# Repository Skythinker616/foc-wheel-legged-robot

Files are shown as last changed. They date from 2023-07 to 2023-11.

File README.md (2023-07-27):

<div align=center>
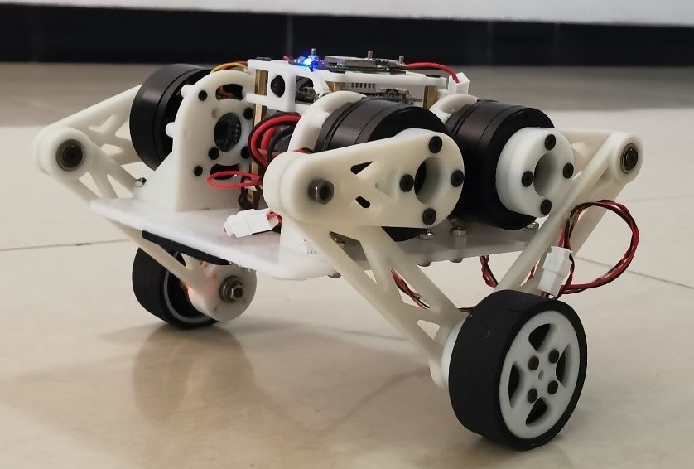
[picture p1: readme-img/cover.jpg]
	
	<h1>FOC 双轮腿机器人项目</h1>
	<p>
		<a href="https://gitee.com/skythinker/foc-wheel-legged-robot">
			
		</a>
		
		<a href="https://github.com/Skythinker616/foc-wheel-legged-robot">
			
		</a>
		
		<a href="https://www.bilibili.com/video/BV1bP411k75b">
			
		</a>
		
	</p>
	<p>
		<b>简体中文 | <a href="README_en.md">English</b></a>
	</p>
</div>

这是一个完整的机器人项目，包含算法仿真、机械结构设计、电子硬件设计、嵌入式软件设计、上位机软件设计等多个部分，完成了以下内容：

- 使用 SolidWorks 完成的机械结构设计
- 基于 MATLAB / Simulink / Simscape 的算法设计和机器人物理仿真
- 基于 STM32，使用 CAN 通信的无刷电机驱动板
- 基于 ESP32、MPU6050 的运动控制模块（主控模块）
- 基于 ffmpeg / ffserver 的 Linux 图传模块，使用低耦合可拔插方案
- 支持蓝牙配网的 Android 遥控 APP

**演示&介绍视频：**[https://www.bilibili.com/video/BV1bP411k75b/](https://www.bilibili.com/video/BV1bP411k75b/)

---

## 部分效果展示

**机械结构渲染图：**

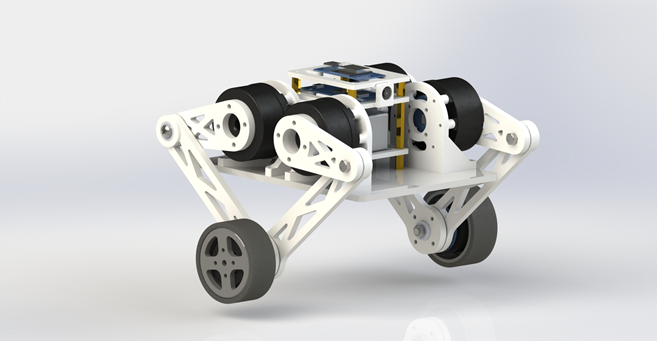
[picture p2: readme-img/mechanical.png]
渲染图


**Simscape Multibody 仿真效果：**

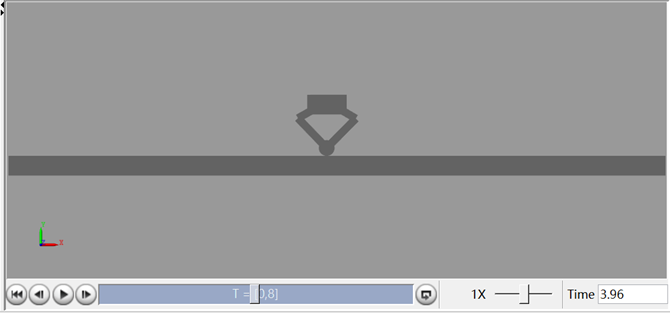
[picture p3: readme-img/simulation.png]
仿真


**机器人加速过程：**

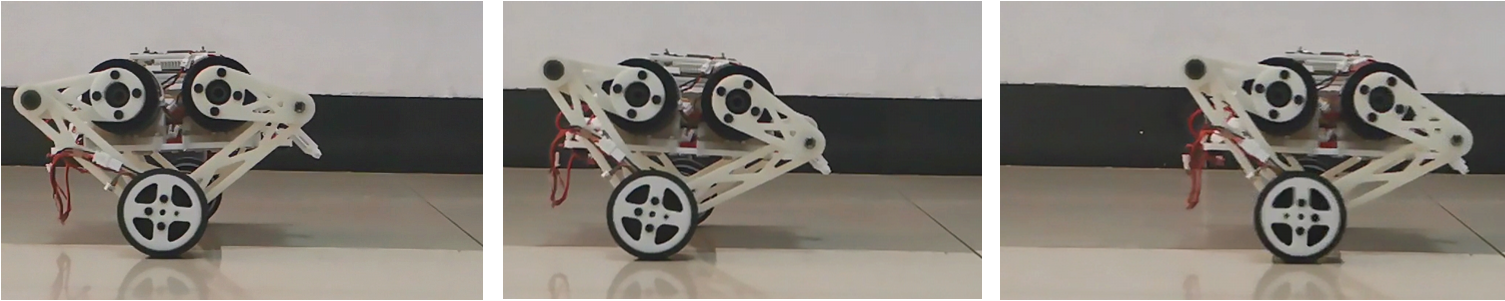
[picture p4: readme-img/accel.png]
加速


**跌落缓冲效果：**

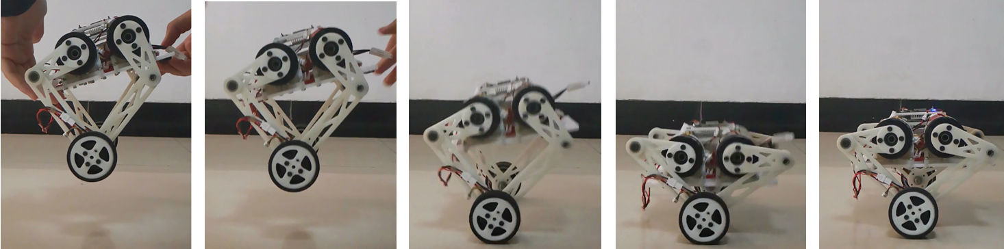
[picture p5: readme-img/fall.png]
跌落


**遥控APP界面：**

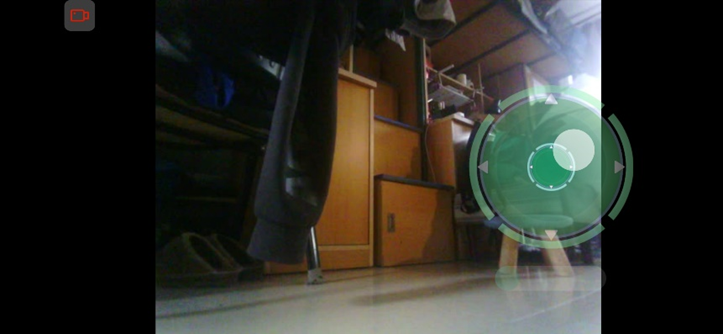
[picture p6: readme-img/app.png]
App


---

## 文件结构

整个机器人项目被分成如下的几个部分，分别位于仓库不同目录下，内部有更详细的说明，读者可以按需查看：

- [`solidworks`](solidworks)：机械结构设计，包含所有零件和总装配体模型文件
- [`matlab`](matlab)：算法仿真，包含模型建立、算法设计和仿真文件等
- [`stm32-foc`](stm32-foc)：无刷电机驱动板，包含硬件设计文件和STM32代码工程
- [`esp32-controller`](esp32-controller)：运动控制模块，包含硬件设计文件和ESP32代码工程
- [`linux-fpv`](linux-fpv)：Linux 图传模块，包含相关Shell脚本和Python脚本
- [`android`](android)：Android 遥控 APP，包含源代码和已编译好的安装包

> 注：图传模块为可选模块，增加可玩性的同时也会明显增加项目的成本和复杂度，删去后其他功能仍可以正常使用

---

## 物料成本

| 项目 | 数量 | 单价 | 总价 |
| :--: | :--: | :--: | :--: |
| 4010电机 | 4 | ￥50.00 | ￥200.00 |
| 2804电机 | 2 | ￥13.00 | ￥26.00 |
| 驱动板元件 | 6 | ￥25.00 | ￥150.00 |
| 主控板元件 | 1 | ￥20.00 | ￥20.00 |
| 航模锂电 | 1 | ￥28.00 | ￥28.00 |
| 3D打印件 | - | 约￥100.00 | 约￥100.00 |
| 定制亚克力 | 1 | ￥5.00 | ￥5.00 |
| 轴承、螺丝 | - | 约￥20.00 | 约￥20.00 |
| 图传核心板（可选） | 1 | ￥150.00 | ￥150.00 |
| 摄像头（可选） | 1 | ￥20.00 | ￥20.00 |
| **总计（不含图传）** | - | - | **￥549.00** |
| **总计（含图传）** | - | - | **￥719.00** |

> 注：以上为笔者实际购买价格，仅供参考，部分购买链接请在各模块的说明中查看

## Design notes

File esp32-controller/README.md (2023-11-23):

# ESP32 主控板

**简体中文 | [English](README_en.md)**

这是本机器人项目最重要的一个子模块，它的职责是：

- 读取板载陀螺仪数据
- 运行所有运动控制算法，包括平衡算法、腿长控制、roll/yaw控制等
- 通过CAN通信获取电机状态并发送扭矩指令
- 通过低功耗蓝牙接收上位机的遥控指令

---

## 硬件说明

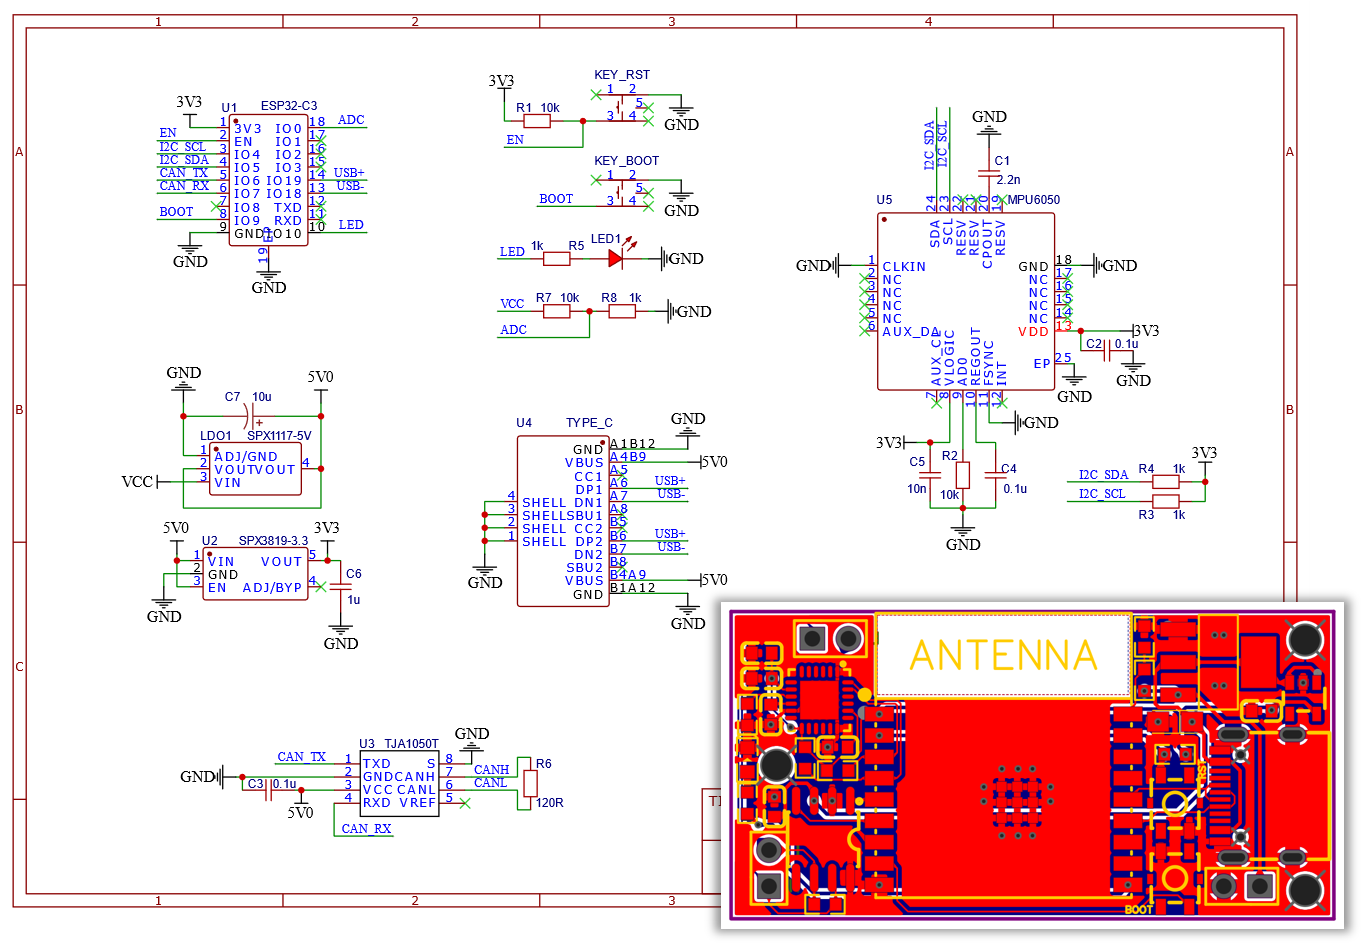
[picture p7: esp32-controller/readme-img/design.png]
电路设计


本模块硬件方案的特性：

- 芯片方案
	- 主控芯片：ESP32-C3
	- 陀螺仪：MPU6050
	- CAN驱动芯片：TJA1050T
- 供电电压：12V，降压方案：LDO
- 调试接口：USB Type-C，直连芯片引脚，可用于烧录程序、JTAG调试和串口通信

### 文件说明

硬件相关文件都在`hardware`目录下：

- `ESP32CTRL_LCEDA_SCH.json`：立创EDA原理图文件
- `ESP32CTRL_LCEDA_PCB.json`：立创EDA PCB文件
- `ESP32CTRL_AD_SCH.schdoc`：立创EDA导出的 Altium Designer 原理图文件
- `ESP32CTRL_AD_PCB.pcbdoc`：立创EDA导出的 Altium Designer PCB文件
- `ESP32CTRL_SVG.svg`：原理图矢量图文件

> 注：将立创原理图和PCB两个json文件导入到[立创EDA标准版](https://lceda.cn/editor)中即可查看和编辑，不建议使用AD

---

## 软件说明

程序使用PlatformIO平台进行开发，使用ESP-IDF并将Arduino框架作为组件引入，因此可同时使用Arduino第三方库和ESP-IDF的底层API(如CAN通信)

为方便程序编写和调试，本程序使用ESP-IDF自带的FreeRTOS进行多任务调度，每个模块会触发一个或多个任务进行处理

### 文件说明

PlatformIO 工程位于`software`目录下，代码文件位于其中`src`目录下：

- `main.cpp`：主要程序文件，包含所有任务模块的逻辑代码
- `PID.c/h`：PID控制器的实现，包含单级和串级PID控制器
- `debug.c/h`：用于[Linkscope](https://gitee.com/skythinker/link-scope)软件实现蓝牙无线调试，不参与正常运行，读者可忽略
- 由MATLAB直接生成的C代码文件，没有可读性，读者可参阅本项目MATLAB程序说明：
	- `leg_pos.c/h`：腿部位置解算函数
	- `leg_spd.c/h`：腿部运动速度解算函数
	- `leg_conv.c/h`：腿部输出换算函数
	- `lqr_k.c/h`：LQR反馈矩阵计算函数

电机、陀螺仪、CAN通信、蓝牙、运动控制等模块的代码全部位于`main.cpp`中（~~其实是偷懒没分开~~），不同模块的函数名基本都以模块名开头，读者可以按此规律参照注释查看

---

## 使用说明

### 烧录程序

使用USB线连接到电脑，按下两个按键后先松开RESET再松开BOOT，芯片即会进入烧录模式，此时可使用PlatformIO进行烧录

### 调试程序

程序中使用Arduinod的Serial类即可从USB输出串口信息，可以使用电脑上的串口调试软件进行查看

此外，ESP32C3的USB还支持JTAG调试，连接到电脑后即可使用[OpenOCD](https://openocd.org/)等程序连接，笔者在调试过程中搭配[Linkscope](https://gitee.com/skythinker/link-scope)实现在线读写变量和曲线绘制，较为方便

### 参数标定

在`main.c`中有几个参数可能需要根据实际系统进行调整，否则将无法进行正确的解算和控制

#### 零点偏移、旋转方向参数

`Motor_InitAll`函数中分别调用`Motor_Init`进行每个电机的参数设定，包括了零点偏移`offsetAngle`和旋转方向`dir`

这两个参数用于在`Motor_Update`函数中将编码器反馈的原始角度转换为算法中的标准角度 $\phi_i$ （电机`angle`成员变量），转换公式为：

$$
\phi_i = (rawAngle_i - offsetAngle_i) * dir_i
$$

这两个参数的测量方法如下：

1. 设置`dir`参数（取值1/-1）使得电机`angle`成员变量在电机向 $\phi_i$ 正方向旋转时增加

2. 程序中设置`offsetAngle=0`（记为 $offsetAngle_i^z$ ），将电机旋转到某个角度，记录当前的计算角度为 $\phi_i^c$ ，测量当前的实际角度为 $\phi_i^r$

3. 将 $\phi_i^c$ 、 $offsetAngle_i^z$ 、 $dir_i$ 代入上方公式，求得 $rawAngle_i$ 的值

4. 将 $\phi_i^r$ 、 $rawAngle_i$ 、 $dir_i$ 代入上方公式，求得 $offsetAngle_i$ 的值，设置到程序中

5. 此时`angle`成员变量应该与实际 $\phi_i$ 一致

> 注1： $\phi_i$ 的定义可以在Matlab程序说明文档中引用的文章中找到，靠前的关节电机对应 $\phi_4$ ，靠后的关节电机对应 $\phi_1$
> 
> 注2：上方描述的均为关节电机，车轮电机仅需设置`dir`参数，使其`angle`变量正方向与算法中驱动轮力矩 $T$ 一致即可

#### 扭矩系数

> 注：若使用笔者相同电机，可以不修改该参数

与上述两个参数相同，该参数也在`Motor_InitAll`函数中进行设置，用于进行电压和扭矩的换算，公式为：

$$
voltage_i = \frac{torque_i}{torqueRatio_i}
$$

其中`torqueRatio`为扭矩系数，其测量方法如下：

1. 给电机不同的电压，测量其扭矩（笔者测的是堵转扭矩），记录为 $(v_i, \tau_i)$
2. 将 $(v_i, \tau_i)$ 拟合为线性函数 $\tau=k*v$ ， $k$ 即为`torqueRatio`的值，可以用Matlab、Excel等软件辅助计算

#### 反电动势函数

> 注：若使用笔者相同电机，可以不修改该参数

关节电机反电动势计算函数为`Motor_CalcRevVolt4010`，车轮电机为`Motor_CalcRevVolt2804`，用于根据电机的实时转速计算反电动势，输出电压指令时会根据计算结果进行补偿，以抵消反电动势

测量反电动势时，给电机不同的电压，测量其空载转速，记录为 $(v_i, \omega_i)$ ，拟合为三次幂函数 $v = f(\omega)$ ，即为反电动势函数

若反电动势标定正确，在设置电机扭矩为0时（`torque`成员为0）手动旋转电机，应该感受到阻力几乎为0（抵消反电动势时顺便抵消了大部分机械阻力）

> 注：注释掉`setup()`中的`Ctrl_Init();`，或注释所有`Motor_SetTorque`函数的调用，即可禁用控制系统的输出，此时可以自行插入代码调试电机

---

## 改进方向

- MPU6050的DMP频率只有200Hz，可以考虑更换其他芯片并编写姿态解算程序
- 硬件使用LDO进行降压，由于ESP32C3功耗较高，LDO发热量较大，可以修改为DC-DC降压
- 关键算法使用MATLAB符号化简结果直接导出，运算量非常大，几乎吃满了芯片性能，无法进一步提升控制频率，可以尝试手动化简后转为C代码

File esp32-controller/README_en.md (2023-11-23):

# ESP32 Main Controller Board

**[简体中文](README.md) | English**

This is the most crucial submodule of the robot project, and its responsibilities include:

- Reading onboard gyroscope data
- Running all motion control algorithms, including balance algorithms, leg length control, roll/yaw control, etc.
- Obtaining motor status via CAN communication and sending torque commands
- Receiving remote control commands from the upper computer through low-power Bluetooth

---

## Hardware Description

Circuit Design

Features of this module's hardware solution:

- Chip Solution
  - Main control chip: ESP32-C3
  - Gyroscope: MPU6050
  - CAN driver chip: TJA1050T
- Power Supply Voltage: 12V, voltage reduction solution: LDO
- Debugging Interface: USB Type-C, directly connected to the chip pins, used for program burning, JTAG debugging, and serial communication

### File Description

Hardware-related files are located in the `hardware` directory:

- `ESP32CTRL_LCEDA_SCH.json`: LCEDA schematic file
- `ESP32CTRL_LCEDA_PCB.json`: LCEDA PCB file
- `ESP32CTRL_AD_SCH.schdoc`: Altium Designer schematic file exported from LCEDA
- `ESP32CTRL_AD_PCB.pcbdoc`: Altium Designer PCB file exported from LCEDA
- `ESP32CTRL_SVG.svg`: Schematic vector file

> Note: Import the two JSON files, the schematic and PCB, into [LCEDA Standard Edition](https://lceda.cn/editor) to view and edit them. It is not recommended to use AD.

---

## Software Description

The program is developed using the PlatformIO platform and uses ESP-IDF, incorporating the Arduino framework as a component. Therefore, it can utilize both Arduino third-party libraries and ESP-IDF's low-level APIs (such as CAN communication).

For ease of program writing and debugging, this program utilizes ESP-IDF's built-in FreeRTOS for multitasking scheduling, and each module will trigger one or more tasks for processing.

### File Description

The PlatformIO project is located in the `software` directory, and the code files are located in the `src` directory:

- `main.cpp`: Main program file, containing the logical code for all task modules
- `PID.c/h`: Implementation of the PID controller, including single-loop and cascade PID controllers
- `debug.c/h`: Used for wireless Bluetooth debugging with [Linkscope](https://gitee.com/skythinker/link-scope) software, not involved in normal operation, readers can ignore it
- C code files generated directly from MATLAB, which are not readable. Readers can refer to the MATLAB program explanation in this project for details:
  - `leg_pos.c/h`: Leg position calculation function
  - `leg_spd.c/h`: Leg motion speed calculation function
  - `leg_conv.c/h`: Leg output conversion function
  - `lqr_k.c/h`: LQR feedback matrix calculation function

The code for motors, gyroscopes, CAN communication, Bluetooth, motion control, and other modules is all located in `main.cpp` (~~I was a bit lazy and didn't separate them~~). The function names of different modules generally start with the module name, and readers can refer to the comments following this pattern to check them.

---

## Instructions for Use

### Program Uploading

Connect the board to the computer via USB, press both buttons, release RESET first, and then release BOOT. The chip will enter the uploading mode, and you can use PlatformIO for uploading.

### Program Debugging

The program uses Arduino's Serial class to output serial information via USB, which can be viewed using serial debugging software on the computer.

In addition, ESP32C3's USB also supports JTAG debugging. After connecting it to the computer, you can use programs like [OpenOCD](https://openocd.org/) to connect. During debugging, I combined it with [Linkscope](https://gitee.com/skythinker/link-scope) for online variable reading, writing, and curve drawing, which is quite convenient.

### Parameter Calibration

Several parameters in `main.c` may need to be adjusted according to the actual system; otherwise, correct computation and control may not be achieved.

#### Zero Offset and Rotation Direction Parameters

In the `Motor_InitAll` function, the `Motor_Init` function is called to set parameters for each motor, including the zero offset `offsetAngle` and rotation direction `dir`.

These two parameters are used in the `Motor_Update` function to convert the raw angle feedback from the encoder to the standard angle $\phi_i$ in the algorithm (motor `angle` member variable). The conversion formula is:

$$
\phi_i = (rawAngle_i - offsetAngle_i) \times dir_i
$$

The measurement methods for these two parameters are as follows:

1. Set the `dir` parameter (values 1/-1) so that the motor `angle` member variable increases when the motor rotates in the positive direction of $\phi_i$.

2. Set `offsetAngle=0` in the program (denoted as $offsetAngle_i^z$), rotate the motor to a certain angle, record the current calculated angle as $\phi_i^c$, and measure the current actual angle as $\phi_i^r$.

3. Substitute $\phi_i^c$, $offsetAngle_i^z$, and $dir_i$ into the above formula to obtain the value of $rawAngle_i$.

4. Substitute $\phi_i^r$, $rawAngle_i$, and $dir_i$ into the above formula to obtain the value of $offsetAngle_i$ and set it in the program.

5. At this point, the `angle` member variable should be consistent with the actual $\phi_i$.

> Note 1: The definition of $\phi_i$ can be found in the article referenced in the Matlab program documentation, where the front joint motor corresponds to $\phi_4$, and the rear joint motor corresponds to $\phi_1`$.
> 
> Note 2: The descriptions above are for joint motors; wheel motors only need to set the `dir` parameter to align their `angle` variable direction with the driving wheel torque $T$ in the algorithm.

#### Torque Coefficient

> Note: If using the same motors as the author, this parameter can be left unchanged.

Similar to the above two parameters, this parameter is also set in the `Motor_InitAll` function and is used for the conversion between voltage and torque. The formula is:

$$
voltage_i = \frac{torque_i}{torqueRatio_i}
$$

Where `torqueRatio` is the torque coefficient, and its measurement method is as follows:

1. Apply different voltages to the motor and measure its torque (the author measured the stall torque), recorded as $(v_i, \tau_i)$.
2. Fit $(v_i, \tau_i)$ to a linear function $\tau=k \times v$. The value of $k$ is the `torqueRatio` and can be calculated using software like Matlab, Excel, etc.

#### Back EMF Function

> Note: If using the same motors as the author, this parameter can be left unchanged.

The back electromotive force calculation function for joint motors is `Motor_CalcRevVolt4010`, and for wheel motors, it is `Motor_CalcRevVolt2804`. It is used to calculate the back electromotive force based on the motor's real-time speed. The output voltage command will be compensated according to the calculation result to counteract the back electromotive force.

When measuring the back electromotive force, apply different voltages to the motor, measure its no-load speed, and record it as $(v_i, \omega_i)$. Fit it to a third-degree polynomial function $v = f(\omega)$, which is the back electromotive force function.

If the back electromotive force calibration is correct, when setting the motor torque to 0 (`torque` member is 0), manually rotating the motor should result in almost zero resistance (when compensating for back electromotive force, most of the mechanical resistance is also compensated).

> Note: Comment out `Ctrl_Init();` in `setup()` or comment out all calls to `Motor_SetTorque` functions to disable the control system's output. This allows for manual insertion of code to debug the motor.

---

## Future Improvements

- The DMP frequency of MPU6050 is only 200Hz; consider replacing it with other chips and writing attitude calculation programs.
- The hardware uses an LDO for voltage reduction, but due to the high power consumption of ESP32C3, the LDO generates a lot of heat. Consider changing to a DC-DC voltage reduction solution.
- Key algorithms directly export results from MATLAB through symbolic simplification, which requires a significant amount of computation and almost saturates the chip's performance, making it impossible to further increase the control frequency. Consider manually simplifying and converting the code to C.

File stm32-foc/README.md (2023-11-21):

# STM32-FOC 电机驱动板

**简体中文 | [English](README_en.md)**

这是本机器人项目的一个子模块，基于 STM32 芯片的无刷电机驱动板，目前有如下特性：

- 芯片方案
	- 主控芯片：STM32F103C6T6
	- 驱动芯片：DRV8313
	- 磁编码器：AS5600
	- CAN驱动芯片：TJA1050T
- 仅支持电压控制扭矩，硬件不支持电流闭环
- 使用 CAN 通信控制（硬件留有串口但程序没有使用）
- 可反馈转角和转速，反馈频率500Hz
- 使用按钮设置电机ID或触发自动标定，产生的参数支持掉电保存
- PCB 尺寸：直径30mm
- 本项目中供电电压：12V
- 物料成本：约￥25

> 注：经测试 STM32F103C8T6 可直接替换，软硬件都可直接兼容

该子模块已经在立创平台开源：[https://oshwhub.com/skythinker/simplefoc103](https://oshwhub.com/skythinker/simplefoc103)

---

## 硬件说明

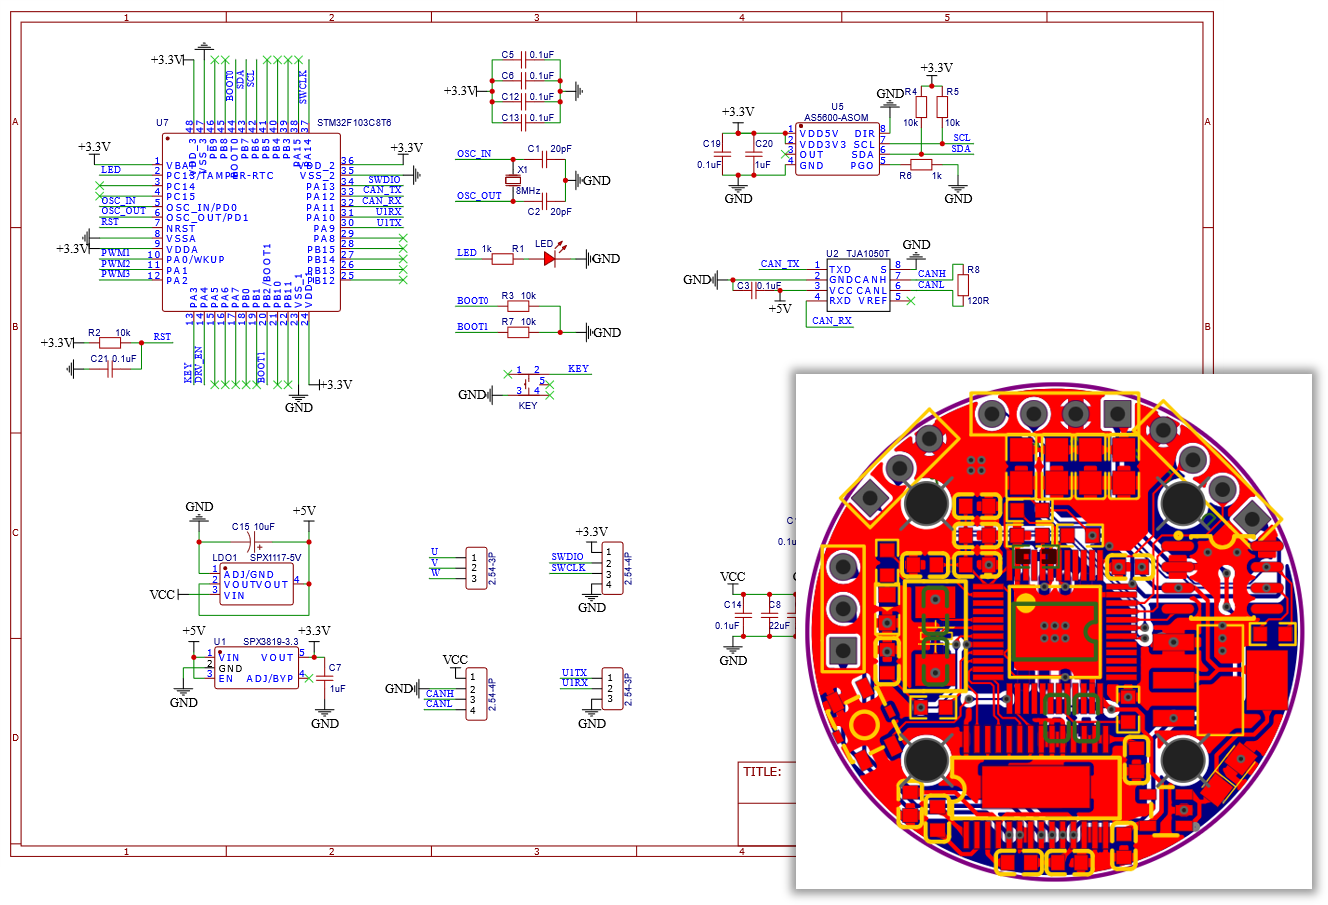
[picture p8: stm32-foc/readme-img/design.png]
电路设计


电路为双层板结构，使用[立创EDA](https://lceda.cn/)设计，其中的对侧打孔相距22mm，与2804电机孔位相同

> 注：程序使用单片机内部RC振荡器，因此外部晶振X1和负载电容C1/C2可以不焊接

### 文件说明

原理图和PCB文件均在`hardware`文件夹中：

- `STM32FOC_LCEDA_SCH.json`：立创EDA原理图文件
- `STM32FOC_LCEDA_PCB.json`：立创EDA PCB文件
- `STM32FOC_AD_SCH.schdoc`：立创导出的 Altium Designer 原理图文件
- `STM32FOC_AD_PCB.pcbdoc`：立创导出的 Altium Designer PCB文件
- `STM32FOC_SVG.svg`：原理图矢量图文件

> 注：将立创原理图和PCB两个json文件导入到[立创EDA标准版](https://lceda.cn/editor)中即可查看和编辑，不建议使用AD

---

## 软件说明

程序开发环境为 Keil uVision 5，使用 STM32CubeMX v5.6.0 生成工程，使用 HAL 库编写

FOC核心算法参考了CSDN博主 [loop222](https://blog.csdn.net/loop222) 所移植的C语言版 SimpleFOC，本程序将其移植到了HAL库中，并添加了CAN通信、Flash掉电存储、蜂鸣、按键、LED、滤波等功能

### 文件说明

`software`文件夹中为STM32代码工程，其中：

- `MDK-ARM/C6T6SimpleFoc.uvprojx`：Keil uVision 5 工程文件
- `C6T6SimpleFoc.ioc`：STM32CubeMX 工程文件
- `Src/main.c`：主要程序代码
- `Src/stm32f1xx_it.c`：各中断服务函数代码
- `USER`目录下为其他工具代码：
	- `BLDCMotor.c/h`、`FOCMotor.c/h`、`foc_utils.c`：FOC算法相关代码
	- `MagneticSensor.c/h`：AS5600磁编码器驱动代码
	- `FlashStorage.c/h`：Flash掉电存储代码

---

## 使用说明

### 硬件设置

1. 将驱动板与电机固定在一起，电机转子上的径向磁铁与磁编码器对正且相距2~3mm

2. 驱动电路板使用2.54mm排针孔引出了电机三相线、CAN总线、电源、SWD调试接口和串口，用户可根据需要自行焊接

	> 注：电源建议选择12V左右，具体范围可以参考DRV8313芯片的电压范围和降压LDO芯片的最高耐压

### 驱动ID设置及自动标定

**驱动ID**：区分一条CAN总线上多个电机的标识，范围1-8，同一总线上的驱动ID不能重复

**自动标定**：驱动需要知道电机的极对数、零点偏移量、传感器方向信息，这些信息可以通过自动标定获得

- 在正常运行状态下，LED的闪烁代表电机当前ID
- 按下按钮不松手即可进入ID设置，此时LED会以500ms周期闪烁，闪烁第N次时松手即可设置ID为N
- 闪烁次数超过8次仍不松手，LED会常亮2秒，此时松手即可进入自动标定
- 若2秒后仍然不松手，LED会熄灭，此后松手不会触发任何操作
- 自动标定时，电机会缓慢旋转，需确保电机处于空载状态，尽可能减少旋转阻力，标定成功后会播放开机音效

### CAN通信协议

CAN通信使用标准帧，波特率为1Mbps

**驱动反馈数据帧格式**：

不同ID的驱动板会使用不同的CAN数据帧标识符(StdID)发送反馈数据：

| 驱动ID | StdID | 帧类型 | DLC |
| :---: | :---: | :----: | :-: |
| N | 0x100+N | 标准帧 | 8 |

| DATA[0-3] | DATA[4-5] | DATA[6-7] |
| :---: | :---: | :---: |
| 累计转角*1000 | 当前转速*10 | 保留 |
| 单位rad | 单位rad/s | / |
| int32_t | int16_t | / |

**驱动板接收电压指令数据帧格式**：

为节省总线带宽，不同ID的驱动板不会使用完全不同的数据帧接收数据，而是共用一个数据帧中的不同字节

共用接收数据帧 **StdID = 0x100** 的四个驱动ID为1-4：

| DATA[0-1] | DATA[2-3] | DATA[4-5] | DATA[6-7] |
| :---: | :---: | :---: | :---: |
| ID=1 输出电压 | ID=2 输出电压 | ID=3 输出电压 | ID=4 输出电压 |
| 单位mV | 单位mV | 单位mV | 单位mV |
| int16_t | int16_t | int16_t | int16_t |

共用接收数据帧 **StdID = 0x200** 的四个驱动ID为5-8：

| DATA[0-1] | DATA[2-3] | DATA[4-5] | DATA[6-7] |
| :---: | :---: | :---: | :---: |
| ID=5 输出电压 | ID=6 输出电压 | ID=7 输出电压 | ID=8 输出电压 |
| 单位mV | 单位mV | 单位mV | 单位mV |
| int16_t | int16_t | int16_t | int16_t |

也就是说，如果向总线发送StdID=0x100的数据帧，那么ID为1-4的驱动板会同时接收到指令；如果发送StdID=0x200的数据帧，则ID为5-8的驱动板会收到指令

> 注意：上述输出电压均为有效值而非峰值，例如供电电压12V时，输出电压允许范围为[0, 6.93V] (12 / √3 = 6.93)

---

## 改进方向

- AS5600磁编码器数据不够稳定，采样频率也不够高(软件IIC实测最高约2KHz)，留给滤波算法的余地不大，可以考虑更换更好的编码器

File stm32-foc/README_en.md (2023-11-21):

# STM32-FOC Motor Driver Board

**[简体中文](README.md) | English**

This is a submodule of the robot project, which is a brushless motor driver board based on the STM32 chip. It currently has the following features:

- Chip solution
  - Main control chip: STM32F103C6T6
  - Driver chip: DRV8313
  - Magnetic encoder: AS5600
  - CAN driver chip: TJA1050T
- Only supports voltage-controlled torque; hardware does not support current closed-loop control
- Uses CAN communication for control (UART is available on the hardware but not utilized in the program)
- Can provide feedback on position and speed with a feedback frequency of 500Hz
- Supports setting the motor ID through a button or triggering automatic calibration, and the generated parameters are saved in non-volatile memory
- PCB size: diameter of 30mm
- Power supply voltage used in this project: 12V
- Material cost: approximately ￥25

> Note: STM32F103C8T6 can be directly replaced and is fully compatible in both software and hardware, as tested.

This submodule has been open-sourced on the oshwhub platform: [https://oshwhub.com/skythinker/simplefoc103](https://oshwhub.com/skythinker/simplefoc103)

---

## Hardware Description

Circuit Design

The circuit is a double-layer board design created using [LCEDA](https://lceda.cn/). The opposite side drilling is spaced at 22mm, which is the same as the 2804 motor mounting holes.

> Note: The program uses the internal RC oscillator of the microcontroller, so the external crystal X1 and load capacitors C1/C2 can be left unpopulated.

### Files Description

The schematic and PCB files are located in the `hardware` folder:

- `STM32FOC_LCEDA_SCH.json`: LCEDA schematic file
- `STM32FOC_LCEDA_PCB.json`: LCEDA PCB file
- `STM32FOC_AD_SCH.schdoc`: Altium Designer schematic file exported from LCEDA
- `STM32FOC_AD_PCB.pcbdoc`: Altium Designer PCB file exported from LCEDA
- `STM32FOC_SVG.svg`: Schematic svg file

> Note: Import the two JSON files, the schematic and PCB, into [LCEDA Standard Edition](https://lceda.cn/editor) to view and edit them. It is not recommended to use AD.

---

## Software Description

The program is developed using Keil uVision 5 as the development environment and generated using STM32CubeMX v5.6.0. It is written using the HAL library.

The FOC core algorithm is based on the C-language version of SimpleFOC, originally ported by CSDN blogger [loop222](https://blog.csdn.net/loop222). This program further integrates it into the HAL library and adds features such as CAN communication, flash memory for non-volatile storage, buzzer, buttons, LEDs, and filtering.

### Files Description

The `software` folder contains the STM32 code project, which includes the following files:

- `MDK-ARM/C6T6SimpleFoc.uvprojx`: Keil uVision 5 project file
- `C6T6SimpleFoc.ioc`: STM32CubeMX project file
- `Src/main.c`: Main program code
- `Src/stm32f1xx_it.c`: Interrupt service routine code
- `USER` folder contains other utility code:
  - `BLDCMotor.c/h`, `FOCMotor.c/h`, `foc_utils.c`: FOC algorithm related code
  - `MagneticSensor.c/h`: AS5600 magnetic encoder driver code
  - `FlashStorage.c/h`: Flash non-volatile memory storage code

---

## Usage Instructions

### Hardware Setup

1. Fix the driver board and the motor together, align the radial magnet on the motor rotor with the magnetic encoder, and keep a distance of 2-3mm.

2. The driver board uses 2.54mm pitch pin headers to expose motor three-phase lines, CAN bus, power supply, SWD debugging interface, and UART. Users can solder them as needed.

> Note: The recommended power supply voltage is around 12V, and the specific range can be referred to the voltage range of the DRV8313 chip and the maximum withstand voltage of the step-down LDO chip.

### Driver ID Setting and Automatic Calibration

**Driver ID**: This is an identifier that distinguishes multiple motors on the same CAN bus, ranging from 1 to 8. The driver IDs on the same bus must not be duplicated.

**Automatic Calibration**: The driver needs to know the pole pairs, zero offset, and sensor direction information of the motor. These pieces of information can be obtained through automatic calibration.

- In normal running state, the LED will blink to indicate the current motor ID.
- To set the ID, press and hold the button. The LED will blink at a 500ms interval. Release the button when the LED blinks for the N-th time to set the ID as N.
- If the button is held for more than 8 blinks, the LED will remain lit for 2 seconds, indicating that automatic calibration will be triggered after releasing the button.
- If the button is not released after 2 seconds, the LED will turn off, and releasing the button will not trigger any action.
- During automatic calibration, the motor will rotate slowly. Ensure that the motor is in an unloaded state and reduce rotational resistance as much as possible. Upon successful calibration, a startup sound effect will be played.

### CAN Communication Protocol

CAN communication uses standard frames with a baud rate of 1Mbps.

**Driver Feedback Data Frame Format**:

Different driver boards with distinct IDs will use different CAN data frame identifiers (StdID) to send feedback data:

| Driver ID | StdID | Frame Type | DLC |
| :---: | :---: | :---: | :-: |
| N | 0x100+N  | Standard | 8 |

| DATA[0-3] | DATA[4-5] | DATA[6-7] |
| :---: | :---: | :---: |
| Accumulated angle \* 1000 | Current speed \* 10 | Reserved |
| Unit: rad | Unit: rad/s | / |
| int32_t | int16_t | / |

**Driver Board Receiving Voltage Command Data Frame Format**:

To save bus bandwidth, driver boards with different IDs will not use entirely different data frames to receive data. Instead, they share the same data frame with different bytes.

The four driver IDs (1-4) share the receive data frame **StdID = 0x100**:

| DATA[0-1] | DATA[2-3] | DATA[4-5] | DATA[6-7] |
| :---: | :---: | :---: | :---: |
| ID=1 Output Voltage | ID=2 Output Voltage | ID=3 Output Voltage | ID=4 Output Voltage |
| Unit: mV | Unit: mV | Unit: mV | Unit: mV |
| int16_t | int16_t | int16_t | int16_t |

The four driver IDs (5-8) share the receive data frame **StdID = 0x200**:

| DATA[0-1] | DATA[2-3] | DATA[4-5] | DATA[6-7] |
| :---: | :---: | :---: | :---: |
| ID=5 Output Voltage | ID=6 Output Voltage | ID=7 Output Voltage | ID=8 Output Voltage |
| Unit: mV | Unit: mV | Unit: mV | Unit: mV |
| int16_t | int16_t | int16_t | int16_t |

In other words, if a data frame with StdID=0x100 is sent on the bus, driver boards with IDs 1-4 will simultaneously receive the command. If a data frame with StdID=0x200 is sent, driver boards with IDs 5-8 will receive the command.

> Note: The above mentioned output voltages are RMS values, not peak values. For example, when the supply voltage is 12V, the allowable range for the output voltage is [0, 6.93V] (12 / √3 = 6.93).

---

## Areas for Improvement

- The AS5600 magnetic encoder data is not stable, and the sampling frequency is not high enough (software I2C measured at a maximum of about 2KHz), leaving little room for filtering algorithms. Consider replacing it with a better encoder.

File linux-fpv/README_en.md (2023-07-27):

# Linux Image Transmission System

**[简体中文](README.md) | English**

This is an optional subsystem in the Robot project, developed on the NanoPI Duo2 development board.

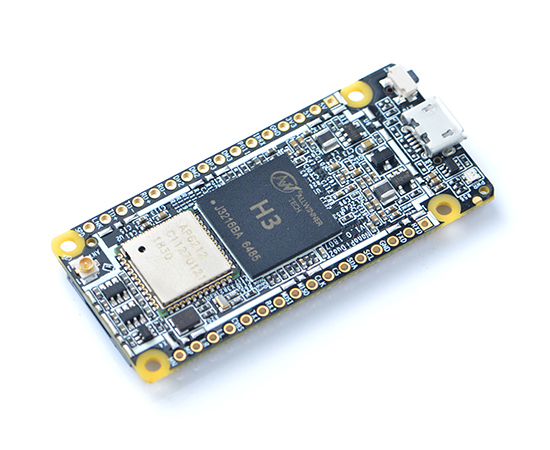
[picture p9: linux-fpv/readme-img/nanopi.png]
NanoPI


The NanoPI Duo2 is a tiny Linux core board measuring 55 x 25.4mm, powered by the Allwinner H3 chip. It supports WiFi and low-power Bluetooth, has a camera interface, and can run either FriendlyCore (based on UbuntuCore) or FriendlyWrt (based on OpenWrt) systems.

The image transmission module of this project is based on the FriendlyCore system (Ubuntu 20.04) of NanoPI Duo2, and it implements the following features:

- Capturing video streams from the ov5640 camera and compressing them into MJPEG format using ffmpeg.
- Streaming the above video stream over HTTP protocol via ffserver for viewing on a mobile app.
- Cooperating with a mobile app to implement Bluetooth pairing, enabling various network connections through the app.
- Creating a UDP server to connect with the mobile app and a Bluetooth GATT client to connect with the main control module, enabling bidirectional data transmission for remote control.

---

## Connection Scheme

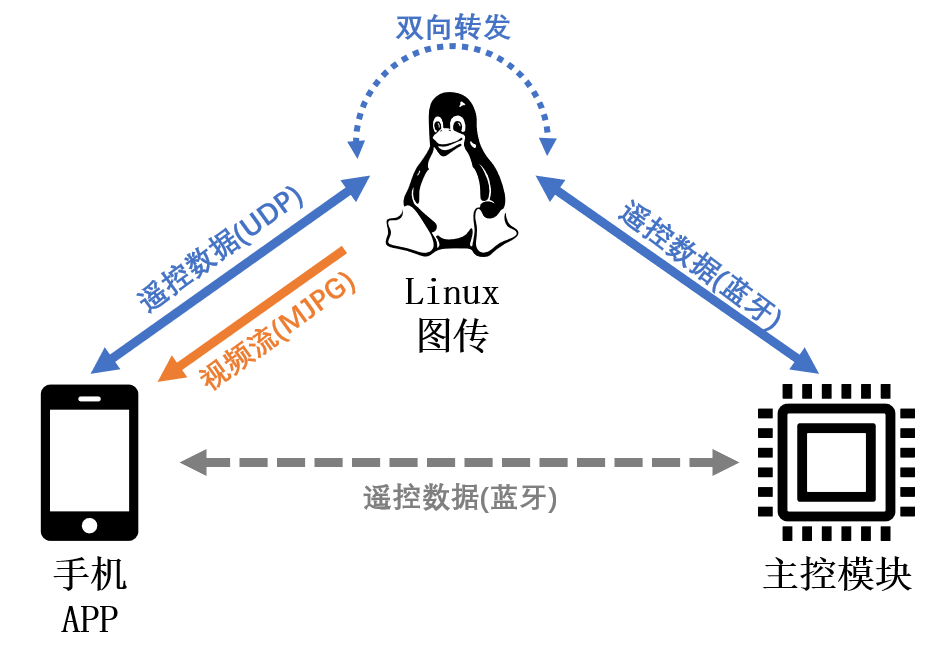
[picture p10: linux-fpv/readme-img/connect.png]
Connection Scheme


The image transmission module implements the plug-and-play scheme shown in the figure above:

- In the scenario of **not using the image transmission system**, the mobile app communicates directly with the main control module via Bluetooth for remote control data transmission (gray arrow).
- In the scenario of **using the image transmission system**, the image transmission system connects with the mobile app through a local area network (LAN) while also connecting with the main control module via Bluetooth. It streams the video (orange arrow) and forwards the remote control data received from the mobile app on the LAN to the main control module (blue arrow). In this case, the robot does not need to be within the range of the mobile app's Bluetooth; it only requires the mobile app and the image transmission system to be on the same LAN.

These two scenarios do not make any difference to the main control module, allowing for flexible switching between different scenarios or complete removal of the image transmission module.

---

## Reference Purchasing Links

> Note: The links below were valid at the time of writing and are for reference only. The availability may vary.

| Item | Purchase Link | Reference Price |
| :--- | :---: | :---: |
| NanoPI Duo2 | [Link](https://item.taobao.com/item.htm?spm=a1z09.2.0.0.67002e8dunEQwK&id=669016013822) | ￥155.00 |
| ov5640 Camera | [Link](https://item.taobao.com/item.htm?spm=a1z09.2.0.0.67002e8dunEQwK&id=676065308445) | ￥20.00 |

---

## Setup Instructions

### 1. Install FriendlyCore System

1. Follow the [official documentation](https://wiki.friendlyelec.com/wiki/index.php/NanoPi_Duo2/zh) to flash the system firmware. The author installed FriendlyCore, based on Linux kernel version 4.14 and Ubuntu 20.04 (focal).

2. Connect the development board to your computer using a USB-to-serial adapter and establish a connection to the board using a serial terminal tool (such as PuTTY). Refer to the official documentation for system login and WiFi network connection.

### 2. Install and Configure ffmpeg and ffserver

1. Download ffmpeg and ffserver from [here](https://ffbinaries.com/downloads). The author used ffmpeg v3.1.4 and ffserver v3.2, and it is recommended to use similar versions.

2. Write the ffserver configuration file by copying the contents from `scripts/ffserver.conf` in this repository to `/etc/ffserver.conf`.

3. Place `scripts/start-ffmpeg.sh` in the system's `/root/balancebot/` directory and run it. Check for any errors. If there are no errors, access `http://<NanoPI's IP address>:8090/camera.mjpg` from another device on the same LAN with a web browser. If you can see the real-time camera stream, the configuration is successful (make sure to connect the camera first).

4. Copy `scripts/mjpg-ffserver.service` to `/lib/systemd/system/` and run the following command:

	```bash
	sudo systemctl daemon-reload
	```

	This will configure the image transmission service as a system service, which can be started or stopped using the following commands:

	```bash
	sudo service mjpg-ffserver start
	sudo service mjpg-ffserver stop
	```

### 3. Configure Python Control Script

1. Ensure that Python 3 is installed on the system. The author used Python 3.8.10 or higher. You can check the Python version using the following command:

	```bash
	python3 --version
	```

2. Install Python dependencies by moving `python/requirements.txt` from the current repository directory to the system, and then run the command:

	```bash
	pip3 install -r requirements.txt
	```

3. Copy the `python/ctrl-proxy.py` file from the repository to the system's `/root/balancebot/` directory. Also, copy the `scripts/ctrl-proxy.service` file to `/lib/systemd/system/`, and run the following command:

	```bash
	sudo systemctl daemon-reload
	```

	This will configure the control script as a system service, which can be started or stopped using the following commands:

	```bash
	sudo service ctrl-proxy start
	sudo service ctrl-proxy stop
	```

4. Set the Python control service to start automatically at boot by running the command:

	```bash
	sudo systemctl enable ctrl-proxy
	```

At this point, the entire image transmission system setup is completed.

---

## Areas for Improvement

- After testing, the current image quality of this solution is 640x480@25fps, and the video delay is approximately 300ms when connected directly to a mobile hotspot. Due to software compression in MJPG format, both CPU and network bandwidth usage are relatively high. You can try using a hardware encoder to compress the video into H264 format and transmit it (the author was not successful in achieving the expected results), or consider using a camera with built-in compression capabilities.

- If image quality is not a concern, you can replace the ffmpeg+ffserver solution with [mjpg-streamer](https://github.com/jacksonliam/mjpg-streamer), which offers easier configuration. However, after testing, it was found that the CPU usage is higher, and without reducing the resolution, it may not achieve a frame rate of 25fps.

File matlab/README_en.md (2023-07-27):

# Model Building & Algorithm Simulation

**[简体中文](README.md) | English**

This project uses MATLAB(R2022b) for the design and simulation of balance algorithms. The main tasks include:

- Leg link posture calculation
- Establishment of the system state space equation
- LQR feedback matrix computation and fitting
- Simscape Multibody physical model construction
- Simulink control algorithm simulation

---

## Control Algorithm

The balance algorithm mainly refers to this [column article](https://zhuanlan.zhihu.com/p/563048952) with only a few differences, hence not elaborated here. It only provides a brief overview of the process, which includes the following steps:

> Note: The variable names in the code remain mostly consistent with those described in the article, and readers can refer to it for comparison.

1. Simplify the leg structure and obtain the mapping relationship between symbols before and after simplification, allowing the calculation of the leg posture using motor data.
2. Determine the mapping relationship between the simplified virtual leg force and the motor torque, enabling control of the simplified leg using the VMC (Virtual Model Control) concept.
3. Conduct classical mechanics analysis and symbolic simplification to obtain the system state space equation.
4. Set the weight coefficients for LQR, calculate the feedback matrix K, and fit the K values for different leg lengths.
5. Implement state feedback control.

---

## File Introduction

- `leg_func_calc.m`: Performs leg kinematics calculations and VMC mapping, which includes steps 1-2 mentioned above, and exports the following three M functions:
	- `leg_pos.m`: Obtains leg posture from joint motor angles.
	- `leg_spd.m`: Obtains leg motion speed from joint motor angles and speeds.
	- `leg_conv.m`: Calculates the torque required by motors from the target torques and thrusts of virtual legs.
- `sys_calc.m`: Computes the system state equation and feedback matrix, which includes steps 3-4 mentioned above, and exports the following M function:
	- `lqr_k.m`: Returns the feedback matrix K corresponding to a specific leg length L0.
- `leg_sim.slx`: Simulink model for leg simulation, including the leg Multibody physical model for verifying the leg VMC algorithm.
	- `leg_sim_2020a.slx`: Exported old version model, suitable for R2020a and above.
- `sys_sim.slx`: Simulink model for the overall balance simulation, including the full robot Multibody physical model for verifying the VMC+LQR overall algorithm.
	- `sys_sim_2020a.slx`: Exported old version model, suitable for R2020a and above.

> Note: The exported M functions are directly used in the simulation model and can be converted to C language using the MATLAB Coder toolbox for direct use in esp32 code. You can find the same-named files in the main control code of this project.

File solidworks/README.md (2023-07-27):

# SolidWorks 机械模型

**简体中文 | [English](README_en.md)**

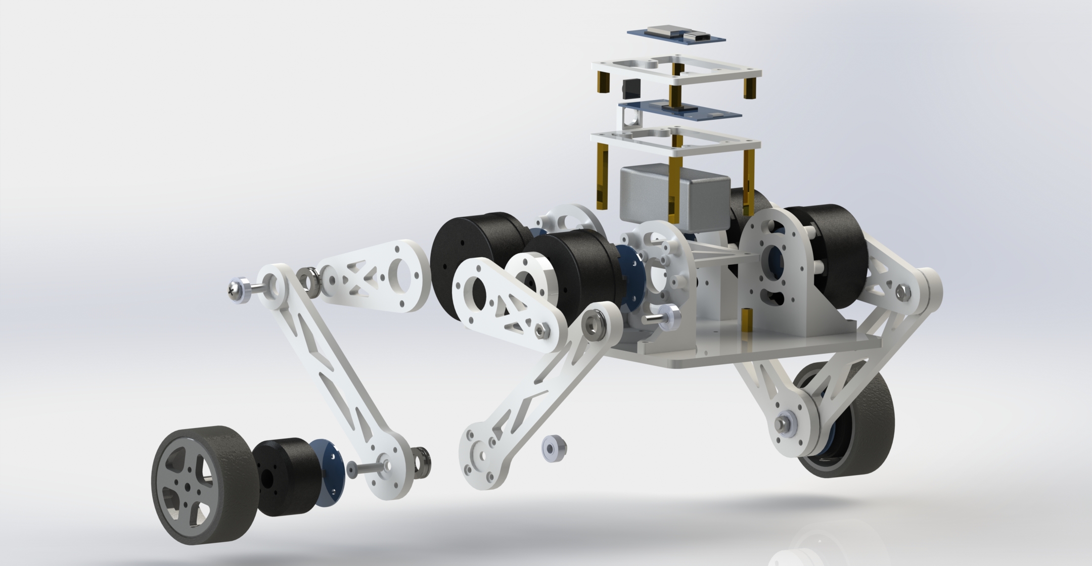
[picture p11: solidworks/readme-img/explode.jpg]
爆炸图


整个机械模型使用SolidWorks 2019 SP0.0设计，当前目录包含所有零件和总装配体`总装.SLDASM`，大部分零件使用3D打印制造，底板为定制亚克力板

---

## 零件选型

> 注：下方的购买链接是笔者当时的购买渠道，仅供参考，不保证可用性

### 电机

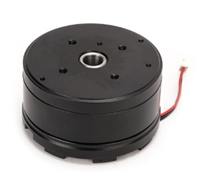
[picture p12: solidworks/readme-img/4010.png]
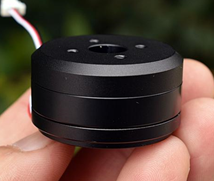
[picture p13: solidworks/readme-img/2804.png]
 

关节电机使用左图所示的4010电机，车轮电机使用右图所示的2804电机，实测电机参数如下：

| 电机型号 | 额定电压 | 堵转扭矩 | 极对数 | 重量 | 购买链接 | 参考价格 |
| :-----: | :---: | :-----: | :----: | :--: | :---: | :---: |
|  4010 |  12V | 0.22N·m | 11 | 125g | [链接](https://item.taobao.com/item.htm?spm=a1z09.2.0.0.67002e8djsrWfk&id=661262833408) | ￥50.00 |
|  2804 |  12V | 0.04N·m | 7 |  24g | [链接](https://item.taobao.com/item.htm?spm=a21n57.1.0.0.54cb523cFK7YX5&id=688692183367) | ￥13.00 |

### 电池

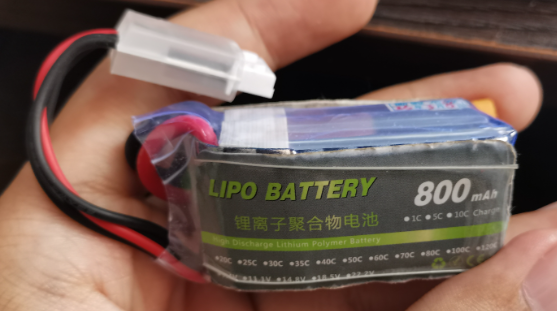
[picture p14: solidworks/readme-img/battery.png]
电池


电池采用了高能量密度高倍率的航模锂电池，实测参数如下：

| 电压 | 容量 | 倍率 | 重量 | 机器人续航 | 购买链接 | 参考价格 |
| :--: | :--: | :--: | :--: | :---: | :---: | :---: |
| 3S (11.1-12.6V) | 800mAh | 25C | 57g | 20-30min | [链接](https://item.taobao.com/item.htm?spm=a1z09.2.0.0.67002e8djsrWfk&id=679306961701) | ￥28.00 | 

### 轴承

在每一个关节处都使用了一个深沟球轴承和一个推力轴承，参数如下：

| 项目 | 内径 | 外径 | 厚度 | 购买链接 | 参考价格 |
| :--: | :--: | :--: | :--: | :---: | :---: |
| 深沟球轴承 604 | 4mm | 12mm| 4mm | [链接](https://item.taobao.com/item.htm?spm=a1z09.2.0.0.67002e8djsrWfk&id=626299304028) | ￥1.30 |
| 推力轴承 F8-14M | 8mm | 14mm | 4mm | [链接](https://item.taobao.com/item.htm?spm=a1z09.2.0.0.67002e8djsrWfk&id=643067962342) | ￥2.00 |

### 螺丝

机器人上使用的大部分都是[扁平头螺丝](https://detail.tmall.com/item.htm?_u=f3m84i7t8421&id=677398679720)，有M2、M2.5、M3、M4几种规格，长度从6mm到16mm不等，有些螺丝没有在模型中画出，需要自行测量（电机上的螺纹盲孔深度为2-3mm）

### 轮胎

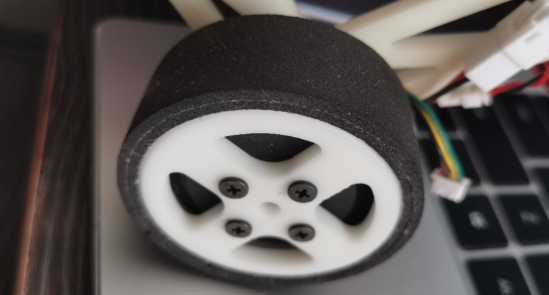
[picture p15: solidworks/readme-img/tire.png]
轮胎


轮胎使用的是自粘海绵胶条，缓冲效果较好，抓地能力较强，但是耐磨性较差，需要定期更换

### 编码器磁铁

电机转子上的磁铁须使用径向充磁的磁铁，由于2804电机不自带磁铁，需要额外设计（本模型选用尺寸直径6mm x 厚度2mm） [购买链接](https://item.taobao.com/item.htm?spm=a1z09.2.0.0.67002e8dunEQwK&id=596454786426) 参考价格：￥6.00 / 5个

### 结构件

机器人底板使用的是白色定制亚克力板 [购买链接](https://detail.tmall.com/item.htm?_u=f3m84i7t207c&id=667937893428) 参考价格：￥5.00

其余全部结构件均在嘉立创使用白色树脂材料打印，全部花费约￥100.00

---

## 改进方向

- 关节电机扭矩无法完成跳跃动作，车轮电机扭矩无法越过较高障碍，可以考虑更换扭矩更大的电机
- 当前电池固定不够牢固，可以增加固定结构
- 车轮电机安装方式 ~~比较阴间~~ 不够方便，可以考虑修改

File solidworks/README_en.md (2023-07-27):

# SolidWorks Mechanical Model

**[简体中文](README.md) | English**

Exploded View

The entire mechanical model is designed using SolidWorks 2019 SP0.0. The current directory contains all parts and the assembly `总装.SLDASM`. Most parts are designed for 3D printing, and the baseplate is made from custom acrylic sheet.

---

## Component Selection

> Note: The purchase links below were used by the author at the time and are provided for reference only. Availability is not guaranteed.

### Motors

 

The articulated joint uses the 4010 motor shown on the left, and the wheel motor uses the 2804 motor shown on the right. The measured motor parameters are as follows:

| Motor Model | Rated Voltage | Stall Torque | Pole Pairs | Weight | Purchase Link | Reference Price |
| :---: | :---: | :---: | :---: | :----: | :---: | :---: |
| 4010 | 12V | 0.22N·m | 11 |  125g  | [Link](https://item.taobao.com/item.htm?spm=a1z09.2.0.0.67002e8djsrWfk&id=661262833408) | ￥50.00 |
| 2804 | 12V | 0.04N·m | 7 |  24g | [Link](https://item.taobao.com/item.htm?spm=a21n57.1.0.0.54cb523cFK7YX5&id=688692183367) | ￥13.00 |

### Battery

Battery

The robot uses a high-energy-density 25C Li-Po batterie. The measured parameters are as follows:

| Voltage | Capacity | Discharge Rate | Weight | Robot Endurance | Purchase Link | Reference Price |
| :-----: | :---: | :---: | :----: | :---: | :---: | :---: |
| 3S (11.1-12.6V) | 800mAh | 25C | 57g  | 20-30min | [Link](https://item.taobao.com/item.htm?spm=a1z09.2.0.0.67002e8djsrWfk&id=679306961701) | ￥28.00 |

### Bearings

A deep groove ball bearing and a thrust bearing are used at each joint, with the following specifications:

| Item | Inner Diameter | Outer Diameter | Thickness | Purchase Link | Reference Price |
| :---: | :---: | :---: | :---: | :---: | :---: |
| Deep Groove Ball Bearing 604 | 4mm | 12mm | 4mm | [Link](https://item.taobao.com/item.htm?spm=a1z09.2.0.0.67002e8djsrWfk&id=626299304028) | ￥1.30 |
| Thrust Bearing F8-14M | 8mm | 14mm | 4mm | [Link](https://item.taobao.com/item.htm?spm=a1z09.2.0.0.67002e8djsrWfk&id=643067962342) | ￥2.00 |

### Screws

Most screws used on the robot are [flat-head screws](https://detail.tmall.com/item.htm?_u=f3m84i7t8421&id=677398679720) with various specifications including M2, M2.5, M3, and M4, with lengths ranging from 6mm to 16mm. Some screws are not depicted in the model and need to be measured independently (the threaded blind holes on the motors are 2-3mm deep).

### Tires

Tire

The robot uses self-adhesive sponge strips as tires, providing good cushioning and strong grip but with relatively poor wear resistance, requiring regular replacement.

### Encoder Magnets

The magnets on the motor rotors must be radially magnetized. Since the 2804 motor does not come with magnets, they need to be designed separately. For this model, magnets with dimensions of 6mm in diameter and 2mm in thickness are used. [Purchase Link](https://item.taobao.com/item.htm?spm=a1z09.2.0.0.67002e8dunEQwK&id=596454786426) Reference Price: ￥6.00 / 5 pieces

### Structural Components

The robot's baseplate is made from custom white acrylic sheet. [Purchase Link](https://detail.tmall.com/item.htm?_u=f3m84i7t207c&id=667937893428) Reference Price: ￥5.00

All other structural components are 3D printed using white resin material from Jialichuang, with a total cost of approximately ￥100.00.

---

## Improvement Directions

- The torque of the articulated joint motor is insufficient for completing jumping actions, and the wheel motor's torque is insufficient for overcoming high obstacles. Consider replacing them with motors having higher torque.
- The current battery fixation is not sturdy enough. Consider adding additional fixation structures.
- The installation method of the wheel motor is not very convenient. Consider making modifications.

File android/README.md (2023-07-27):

# Android App

**简体中文 | [English](README_en.md)**

这是本机器人项目的一个子模块，基于Android Studio开发，有以下功能：

- 读取用户触摸输入，向机器人发送遥控指令
- 拉取图传系统的视频流显示在界面上
- 配合图传系统进行蓝牙配网

界面效果

---

## 实现方案

### 显示方案

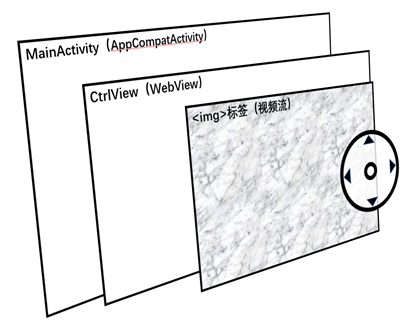
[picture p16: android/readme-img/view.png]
界面层级


由于图传系统传来的MJPG视频流可以直接在各种浏览器中访问，因此本程序直接重写了一个WebView作为主显示视图，仅需编写少量HTML+JavaScript代码即可实现视频流的显示

同时，程序重写了WebView的onDraw方法，在HTML页面上方叠加绘制了摇杆、滑块等控件，并通过onTouchEvent方法监听用户的触摸输入

### 图传连接方案

关于图传系统的通信链路，请先参阅[图传系统方案](../linux-fpv/README.md#连接方案)

为了连接到图传系统，需要通过网络建立视频流连接和UDP遥控数据链接，如下图所示时序：

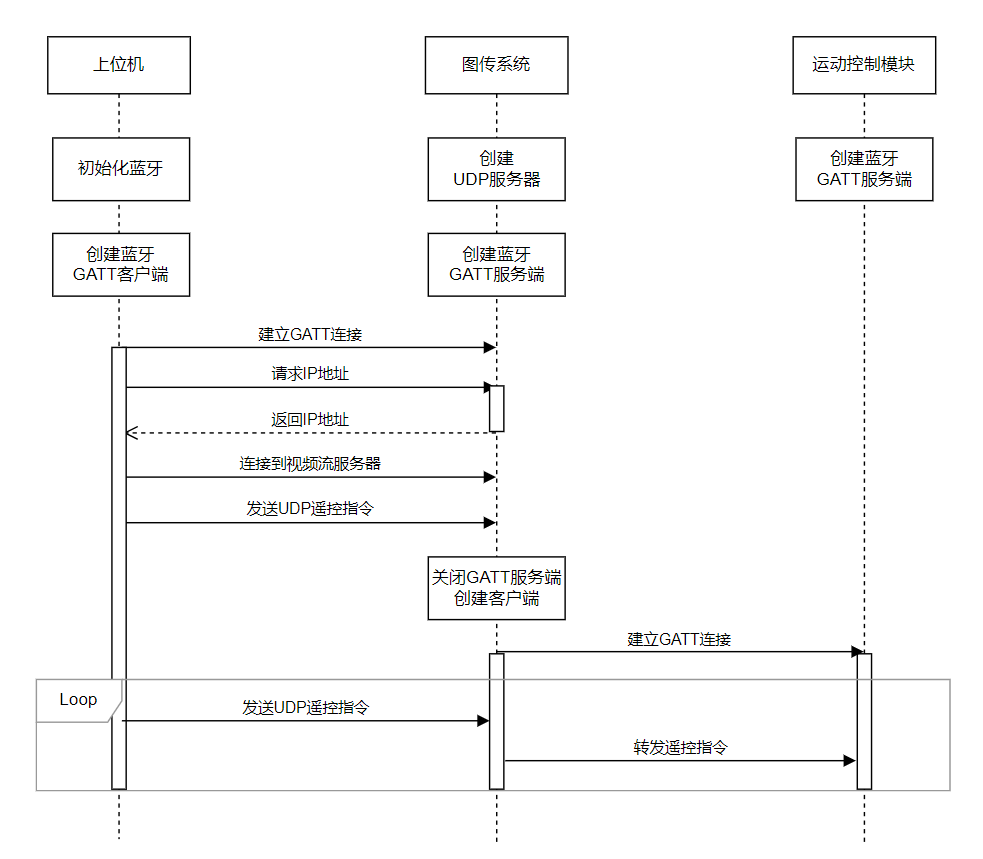
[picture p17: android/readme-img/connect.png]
连接时序


> 注：图中“上位机”表示本程序，“运动控制模块”表示机器人主控模块

### 蓝牙配网方案

蓝牙配网指的是本程序先通过蓝牙直接连接到图传系统，向其发送网络信息，使其连接到指定的WiFi网络，此后即可通过网络连接到图传系统，整个过程都是自动完成的，如下图所示时序：

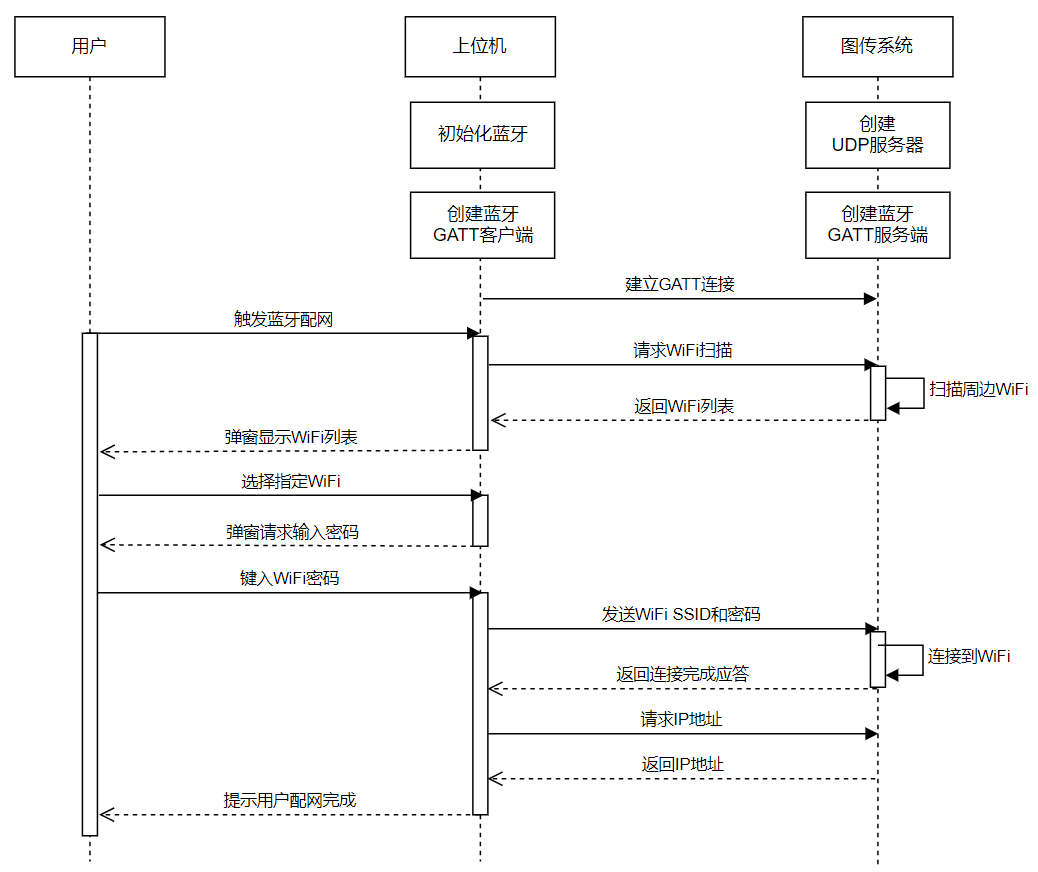
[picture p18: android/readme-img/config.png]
蓝牙配网时序


---

## 主要文件

- `balancebot.apk`：已编译好的安装包，可直接安装
- `app/src/main/java/com/skythinker/balancebot`：Java源代码
	- `MainActivity.java`：主Activity，负责创建各模块对象，接收事件并发送遥控指令
	- `Bluetooth.java`：蓝牙模块，负责蓝牙连接、数据收发
	- `WifiClient.java`：WiFi客户端模块，负责创建UDP客户端并收发数据
	- `CtrlView.java`：主视图，重写自WebView，负责绘制界面
- `app/src/main/AndroidManifest.xml`：Android清单文件，声明了程序的权限和Activity
- `app/src/main/res/drawable`：各图片资源
- `app/src/main/assets/streamview.html`：显示视频流的WebView页面

---

## 使用说明

1. 给机器人上电，等待图传系统启动完成(约1min)

2. 打开本程序，点击左上角的配置按钮

	- 如果不使用图传，点选“切换到蓝牙模式”，等待连接成功
	- 如果使用图传，点选“切换到图传模式”，然后再次点击配置按钮选择“进行连接配置”，按要求选择网络并输入密码，等待连接成功

3. 左上角配置按钮由灰色变亮即表示连接成功，此时即可使用摇杆控制机器人

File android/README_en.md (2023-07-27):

# Android App

**[简体中文](README.md) | English**

This is a sub-module of the Robot Project, developed using Android Studio, and it provides the following functionalities:

- Reads user touch inputs to send remote control commands to the robot.
- Pulls and displays the video stream from the image transmission system on the interface.
- Cooperates with the image transmission system for Bluetooth pairing.

Interface Preview

---

## Implementation Approach

### Display Solution

Interface Hierarchy

Since the MJPG video stream from the image transmission system can be directly accessed in various browsers, this application directly utilizes a WebView as the main display view. Only a small amount of HTML+JavaScript code is needed to display the video stream.

Additionally, the application overrides the onDraw method of WebView to overlay controls such as joystick and sliders on top of the HTML page, and it uses the onTouchEvent method to listen for user touch inputs.

### Image Transmission Connection Solution

Regarding the communication link of the image transmission system, please refer to [Image Transmission System Solution](../linux-fpv/README_en.md#Connection%20Scheme) first.

To connect to the image transmission system, a video stream connection and UDP remote control data link need to be established over the network. The following timing diagram illustrates the process:

Connection Timing

> Note: In the diagram, "Upper Computer" represents this application, and "Motion Control Module" represents the robot's main control module.

### Bluetooth Pairing Solution

Bluetooth pairing refers to this application establishing a direct Bluetooth connection with the image transmission system, sending network information to connect it to the specified WiFi network. Afterward, the application can connect to the image transmission system over the network automatically. The following timing diagram illustrates the process:

Bluetooth Pairing Timing

---

## Important Files

- `balancebot.apk`: Pre-compiled installation package for direct installation.
- `app/src/main/java/com/skythinker/balancebot`: Java source code.
	- `MainActivity.java`: Main Activity responsible for creating various module objects, receiving events, and sending remote control commands.
	- `Bluetooth.java`: Bluetooth module responsible for Bluetooth connection and data transmission.
	- `WifiClient.java`: WiFi client module responsible for creating UDP client and handling data transmission.
	- `CtrlView.java`: Main view, overrides WebView, responsible for UI drawing.
- `app/src/main/AndroidManifest.xml`: Android manifest file, declaring the program's permissions and activities.
- `app/src/main/res/drawable`: Various image resources.
- `app/src/main/assets/streamview.html`: WebView page for displaying the video stream.

---

## Usage Instructions

1. Power on the robot and wait for the image transmission system to start up (approximately 1 minute).

2. Open this application and click the configuration button in the top-left corner.

	- If not using image transmission, select "Switch to Bluetooth mode" and wait for a successful connection.
	- If using image transmission, select "Switch to image transmission mode," then click the configuration button again, and choose "Configure connection" as instructed. Select the network and enter the password as required, and wait for a successful connection.

3. The configuration button in the top-left corner will become active (from gray to lit) when the connection is successful. At this point, you can use the joystick to control the robot.

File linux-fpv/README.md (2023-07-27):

# Linux 图传系统

**简体中文 | [English](README_en.md)**

这是本机器人项目中的一个可选子系统，基于NanoPI Duo2开发板进行开发

NanoPI

这是一块 55 x 25.4mm 的非常小巧的Linux核心板，使用全志H3芯片，支持WiFi和低功耗蓝牙，引出了摄像头接口，可以运行FriendlyCore系统(基于UbuntuCore)或FriendlyWrt系统(基于OpenWrt)

本项目的图传子模块基于其FriendlyCore系统(Ubuntu 20.04)进行开发，实现了以下功能：

- 通过ffmpeg采集ov5640摄像头的视频流并压缩为mjpeg格式
- 通过ffserver将上述视频流以HTTP协议进行推流，以便在手机APP中收看
- 与手机APP配合实现蓝牙配网，在手机端操作即可连接各种网络
- 创建UDP服务端与手机APP连接，创建蓝牙GATT客户端与主控模块连接，实现遥控数据双向转发

---

## 连接方案

连接方案

图传模块实现了上图所示的可拔插方案：

 - 在**不使用图传系统**的情况下，手机APP与主控模块通过蓝牙直连进行遥控数据传输(灰色箭头)
 - 在**使用图传系统**的情况下，图传系统与手机通过局域网连接，同时通过蓝牙与主控模块连接，在传输视频流(橙色箭头)的同时，将手机从局域网传来的遥控数据转发到主控模块(蓝色箭头)。此时机器人不需要在手机蓝牙范围内，仅需保证手机与图传系统在同一局域网内即可

这两种情况对于主控模块没有任何区别，因此可以在不同的场景下灵活切换，也可以完全移除图传模块

---

## 参考购买途径

> 注：下方的链接是笔者当时的购买链接，仅供参考，不保证可用性

| 项目 | 购买链接 | 参考价格 |
| :--: | :---: | :---: |
| NanoPI Duo2 | [链接](https://item.taobao.com/item.htm?spm=a1z09.2.0.0.67002e8dunEQwK&id=669016013822) | ￥155.00 |
| ov5640摄像头 | [链接](https://item.taobao.com/item.htm?spm=a1z09.2.0.0.67002e8dunEQwK&id=676065308445) | ￥20.00 |

---

## 搭建方法

### 1. 安装FriendlyCore系统

1. 参照[官方文档](https://wiki.friendlyelec.com/wiki/index.php/NanoPi_Duo2/zh)进行系统固件的烧录，笔者安装的是基于Linux内核版本4.14和Ubuntu 20.04(focal)的FriendlyCore系统

2. 使用USB转串口模块将开发板连接到电脑，使用串口终端工具(如PuTTY)连接到开发板，参照官方文档登录系统并连接到WiFi网络

### 2. 安装并配置ffmpeg和ffserver

1. 下载ffmpeg和ffserver [下载地址](https://ffbinaries.com/downloads)，笔者使用的是ffmpeg v3.1.4和ffserver v3.2，建议使用相近版本

2. 编写ffserver配置文件，将本仓库目录`scripts/ffserver.conf`中的内容复制到`/etc/ffserver.conf`中

3. 将`scripts/start-ffmpeg.sh`放在系统`/root/balancebot/`目录下并运行，查看是否报错，若不报错，从同一局域网下的其他设备上用浏览器访问`http://<NanoPI的IP地址>:8090/camera.mjpg`，若能看到摄像头的实时画面，则说明配置成功(记得先插上摄像头)

4. 将`scripts/mjpg-ffserver.service`复制到`/lib/systemd/system/`下，运行命令：

	```bash
	sudo systemctl daemon-reload
	```

	即可将图传指令配置为系统服务，可以通过下述命令进行启动或停止
	
	```bash
	sudo service mjpg-ffserver start
	sudo service mjpg-ffserver stop
	```

### 3. 配置Python控制脚本

1. 确定系统已经安装Python3，笔者使用的是Python 3.8.10，建议使用相近或更高版本。可以使用以下命令查看Python版本：

	```bash
	python3 --version
	```

2. 安装Python依赖库，将当前仓库目录下`python/requirements.txt`移至系统中，运行命令：

	```bash
	pip3 install -r requirements.txt
	```

3. 将仓库中`python/ctrl-proxy.py`文件复制到系统`/root/balancebot/`目录下，再将`scripts/ctrl-proxy.service`文件复制到`/lib/systemd/system/`下，运行命令：

	```bash
	sudo systemctl daemon-reload
	```

	即可将该控制脚本配置为系统服务，可以通过下述命令进行启动或停止
	
	```bash
	sudo service ctrl-proxy start
	sudo service ctrl-proxy stop
	```

4. 将Python控制服务设置为开机自启动，运行命令：

	```bash
	sudo systemctl enable ctrl-proxy
	```

此时已经完成整个图传系统的搭建

---

## 改进方向

- 经测试，本方案图传画质为640x480@25fps，直连手机热点时画面延迟约300ms，由于使用软件压缩为MJPG格式，CPU和网络带宽占用都比较高，可以尝试调用硬件编码器压缩为H264格式并传输(笔者没有成功达到预期效果)，或换用内置压缩功能的摄像头

- 不考虑图像画质的话，可以将ffmpeg+ffserver方案直接更换为[mjpg-streamer](https://github.com/jacksonliam/mjpg-streamer)方案，配置更为方便，但经测试CPU占用更高，不降分辨率的话无法达到25fps帧率

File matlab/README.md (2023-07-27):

# 模型搭建&算法仿真

**简体中文 | [English](README_en.md)**

本项目使用 MATLAB(R2022b) 进行平衡算法的设计和仿真，主要进行了：

- 腿部连杆姿态计算
- 系统状态空间方程建立
- LQR 反馈矩阵计算和拟合
- Simscape Multibody 物理模型搭建
- Simulink 控制算法仿真

---

## 控制算法

平衡算法主要参考了这个[专栏文章](https://zhuanlan.zhihu.com/p/563048952)，仅有少许不同，因此不在此处详述，仅描述大致过程，包含以下几个步骤：

> 注：代码中变量名称与该文章所述基本保持一致，读者可以对照查看

1. 对腿部结构进行化简，求得化简前后各符号的对照关系，从而可以使用电机数据计算出腿部的姿态
2. 求得化简后的虚拟腿受力到电机扭矩的映射关系，从而可以使用VMC思想对化简后的腿部进行控制
3. 进行经典力学分析和符号化简，求得系统状态空间方程
4. 设定LQR中的权重系数，求取反馈矩阵K，并对不同腿长求出的K进行拟合
5. 进行状态反馈控制

---

## 文件介绍

- `leg_func_calc.m`：进行腿部解算和 VMC 映射计算，包含上述步骤1-2，导出以下三个M函数：
	- `leg_pos.m`：可由关节电机角度求得腿部姿态
	- `leg_spd.m`：可由关节电机角度速度求得腿部运动速度
	- `leg_conv.m`：可由虚拟腿目标扭矩和推力求得电机所需输出的力矩
- `sys_calc.m`：求得系统状态方程，求得反馈矩阵，包含上述步骤3-4，导出下述M函数：
	- `lqr_k.m`：代入腿长 L0 后返回该腿长对应的反馈矩阵 K
- `leg_sim.slx`：腿部仿真 Simulink 模型，包含腿部 Multibody 物理模型，用于腿部VMC算法验证
	- `leg_sim_2020a.slx`：导出的旧版本模型，适用 R2020a 及以上版本
- `sys_sim.slx`：整机平衡仿真 Simulink 模型，包含整机 Multibody 物理模型，用于 VMC+LQR 整体算法验证
	- `sys_sim_2020a.slx`：导出的旧版本模型，适用 R2020a 及以上版本

> 注：导出的M函数都在仿真模型中直接使用，使用 MATLAB Coder 工具箱直接转换为C语言后即可直接在实机代码中使用，在本项目主控代码中可以找到同名文件

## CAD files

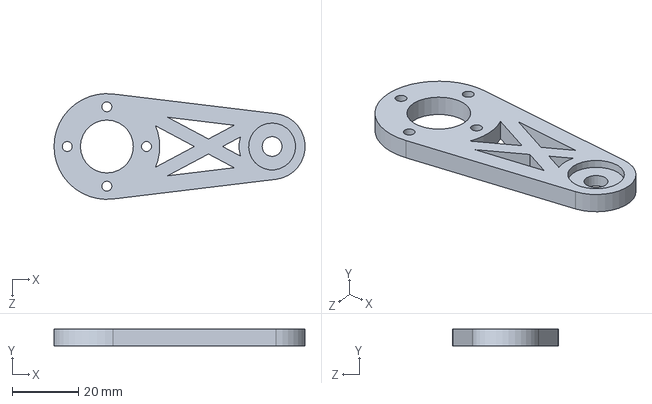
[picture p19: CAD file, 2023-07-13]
solidworks/大腿.SLDPRT
76.0 x 5.00 x 32.0 mm

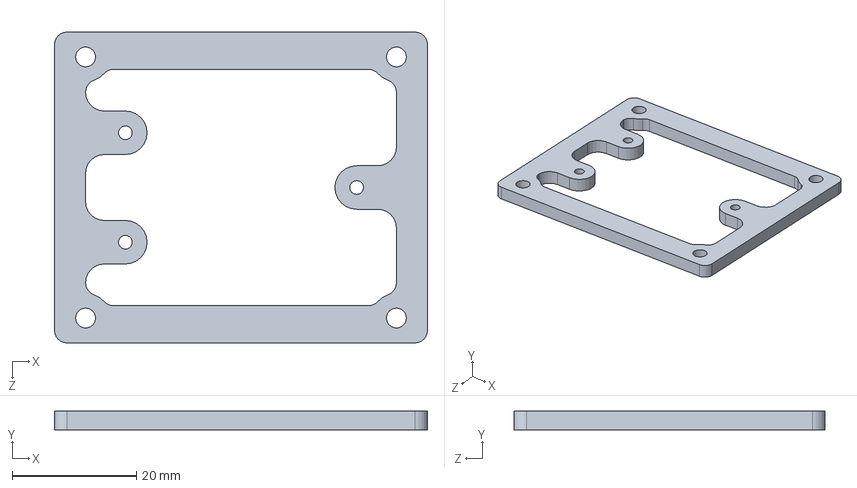
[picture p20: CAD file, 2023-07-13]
solidworks/主控支架.SLDPRT
60.0 x 3.00 x 50.0 mm

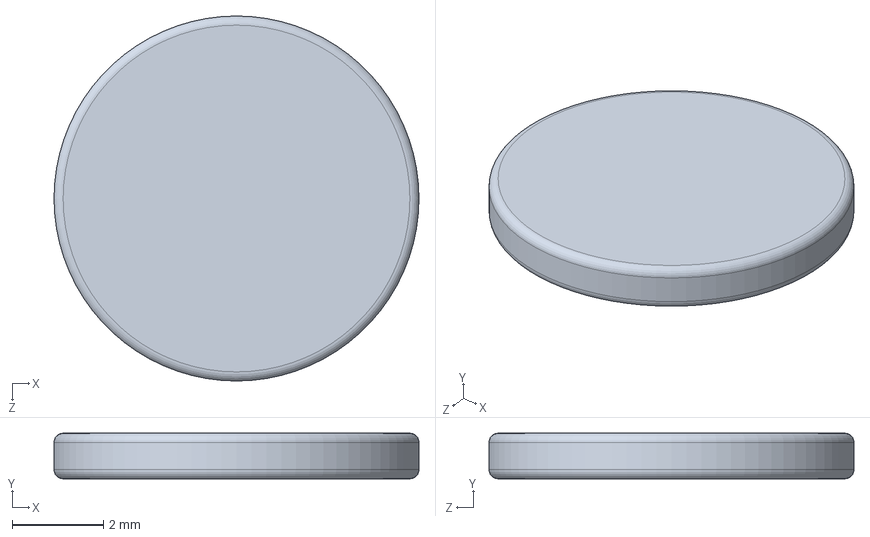
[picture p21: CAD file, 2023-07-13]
solidworks/编码器磁铁.SLDPRT
8.00 x 1.00 x 8.00 mm

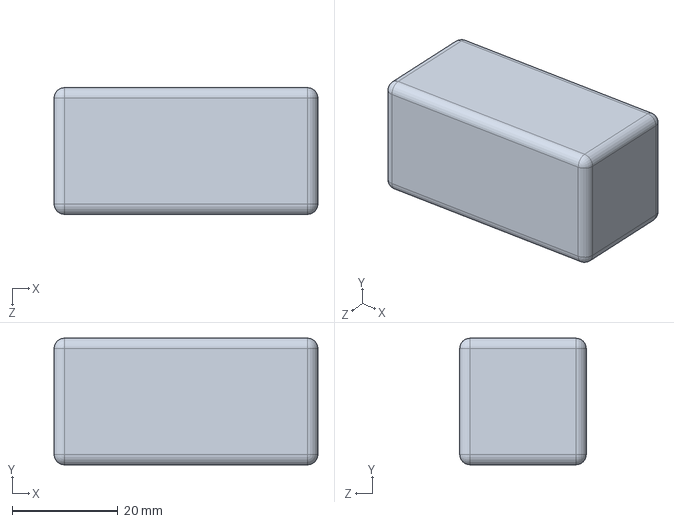
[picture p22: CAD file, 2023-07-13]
solidworks/动力锂电池.SLDPRT
50.0 x 24.0 x 24.0 mm

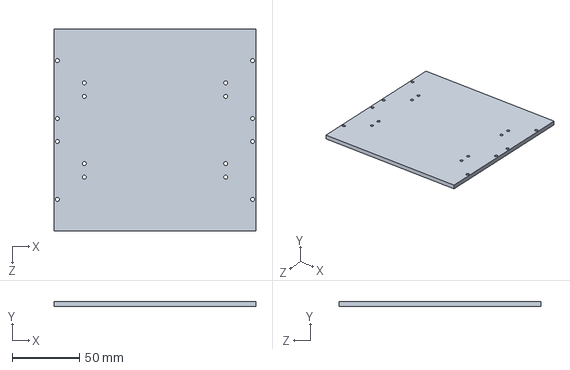
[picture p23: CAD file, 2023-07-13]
solidworks/底板.SLDPRT
150.0 x 4.00 x 150.0 mm

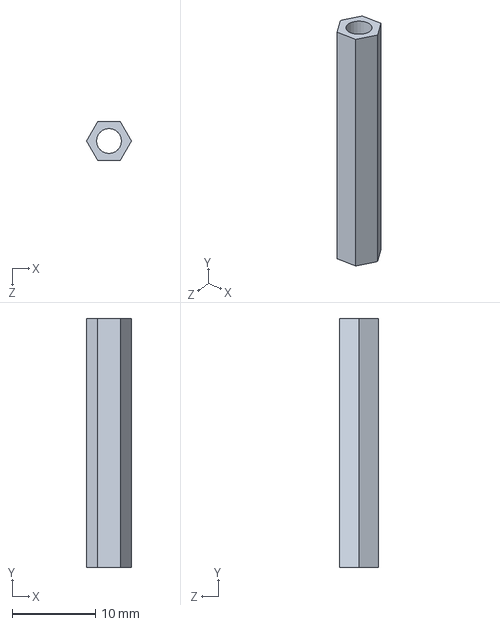
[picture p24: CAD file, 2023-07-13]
solidworks/主控支撑铜柱.SLDPRT
5.43 x 30.0 x 4.70 mm

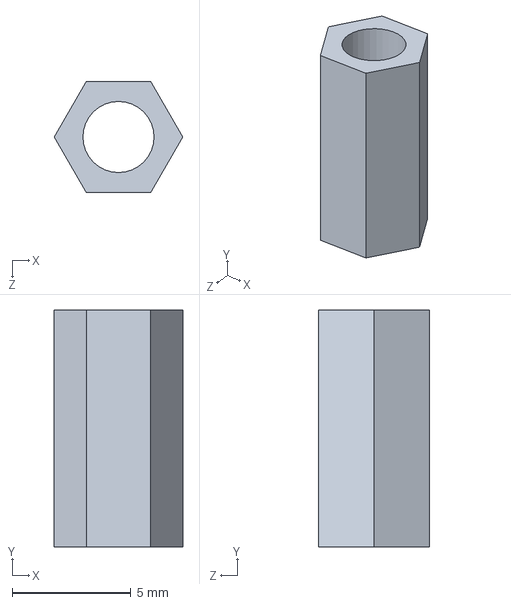
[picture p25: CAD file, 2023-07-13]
solidworks/电池支撑铜柱.SLDPRT
5.43 x 10.0 x 4.70 mm

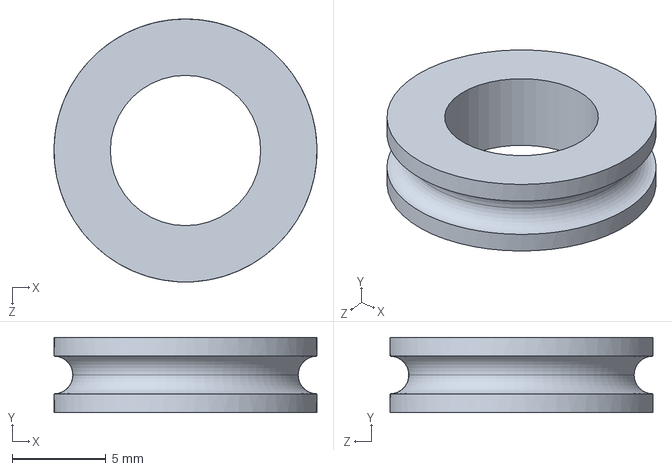
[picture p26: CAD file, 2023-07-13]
solidworks/推力轴承.SLDPRT
14.0 x 4.00 x 14.0 mm

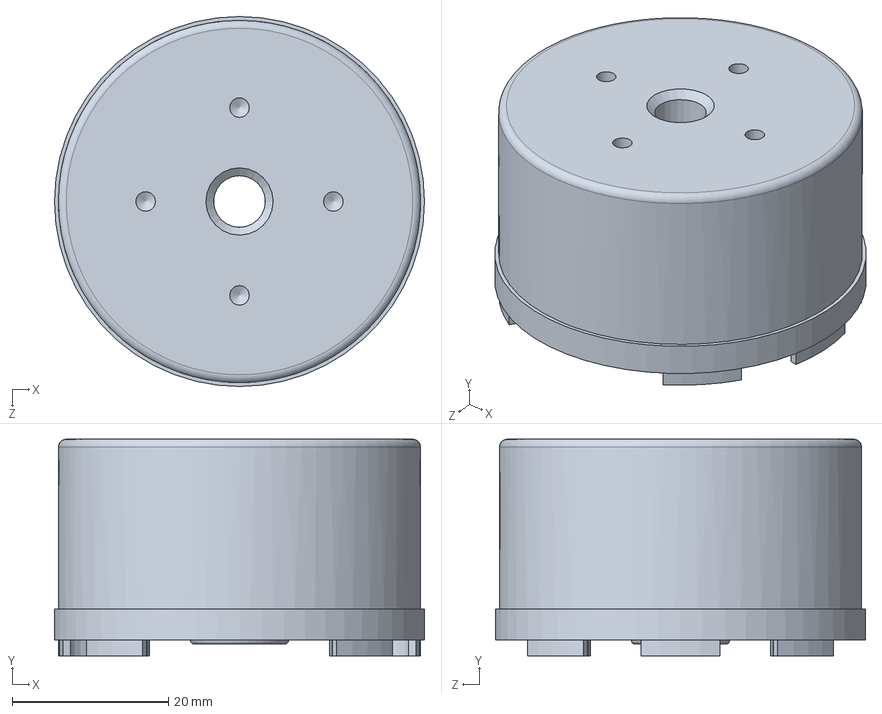
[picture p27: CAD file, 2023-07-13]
solidworks/4010电机.SLDPRT
47.3 x 27.7 x 47.3 mm

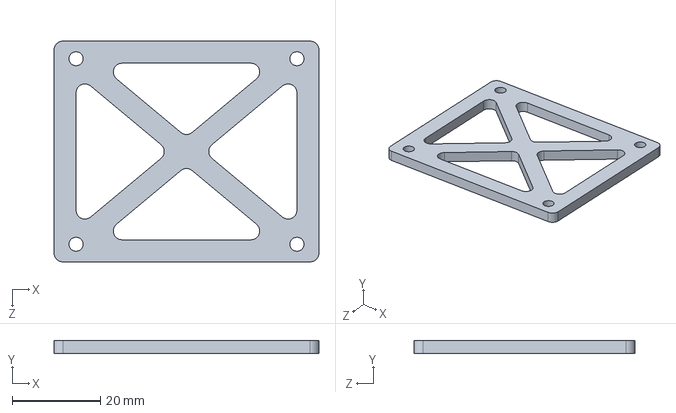
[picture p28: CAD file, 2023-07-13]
solidworks/电池架.SLDPRT
60.0 x 3.00 x 50.0 mm

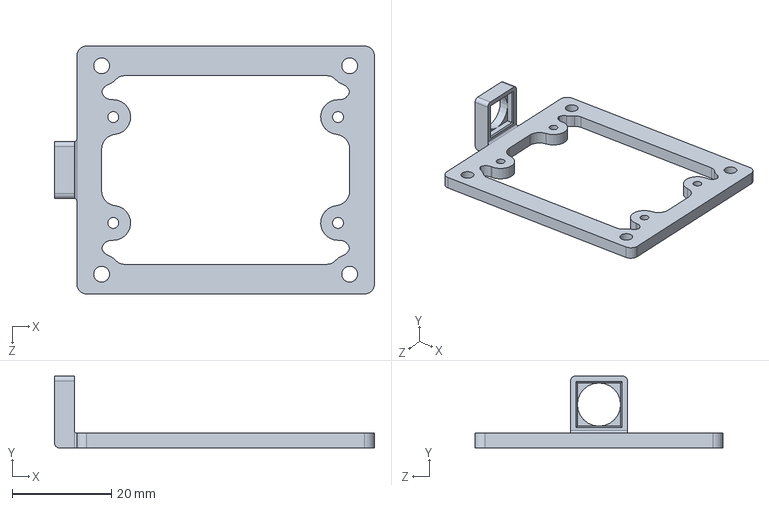
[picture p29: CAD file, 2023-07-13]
solidworks/NanoPi支架.SLDPRT
64.5 x 14.5 x 50.0 mm

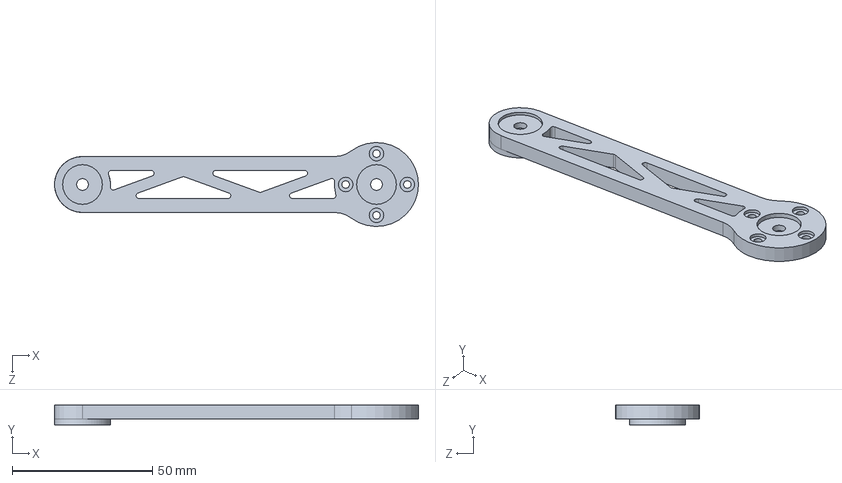
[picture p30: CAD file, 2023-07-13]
solidworks/小腿.SLDPRT
130.0 x 7.00 x 30.0 mm

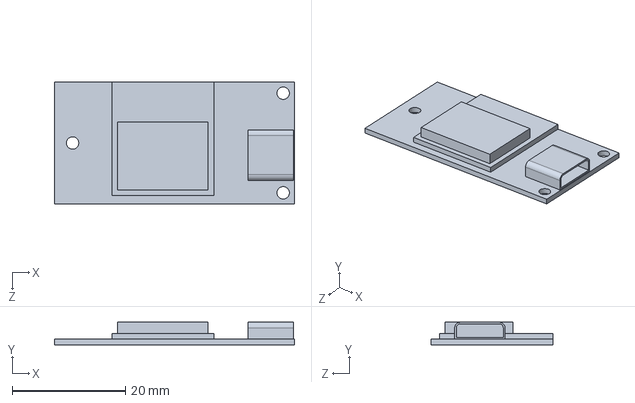
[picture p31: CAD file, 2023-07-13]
solidworks/主控板PCB.SLDPRT
42.4 x 4.00 x 21.6 mm

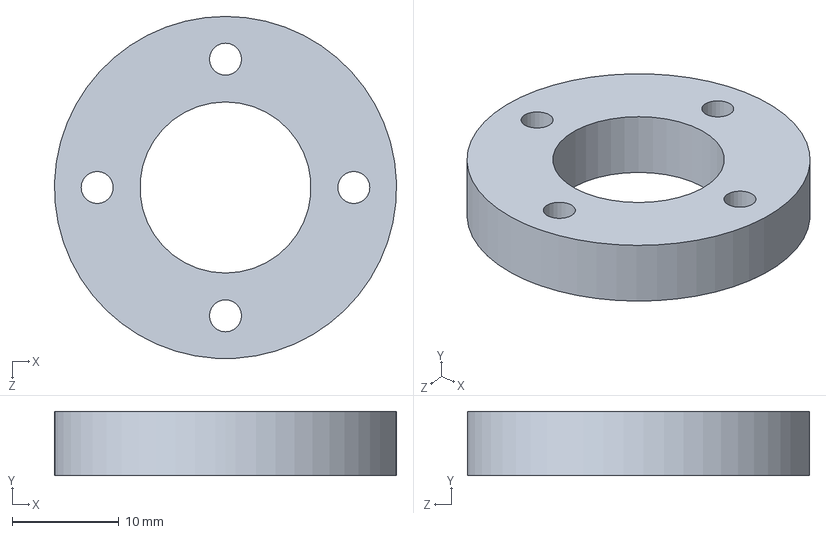
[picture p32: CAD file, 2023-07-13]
solidworks/大腿垫高.SLDPRT
32.0 x 6.00 x 32.0 mm

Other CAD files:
solidworks/OV5640镜头.SLDPRT
solidworks/hex nuts, style 1-grades ab gb.sldprt
solidworks/车轮.SLDPRT
solidworks/2804电机.SLDPRT
solidworks/MISUMI_C-SE604ZZ_不锈钢小径滚珠轴承.SLDPRT
solidworks/MISUMI_CBSTSR4-16_内六角螺栓（盖螺栓）.SLDPRT
solidworks/NanoPi.SLDPRT
solidworks/cross recessed pan head screws gb.sldprt
solidworks/关节电机支架.SLDPRT
solidworks/轮胎.SLDPRT
solidworks/驱动板.SLDPRT

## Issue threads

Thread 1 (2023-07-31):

vTaskDelayUntil() 在CAN_RecvTask()中的调用目前没有效果,会立即返回（Bug）

Tony607, 2023-07-31:
https://github.com/Skythinker616/foc-wheel-legged-robot/blob/e14c90cd661c82906f52846733aca11bd062f9d9/esp32-controller/software/src/main.cpp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
`xLastWakeTime`在循环中没有被更新。因此`xLastWakeTime`保持在初始值。`vTaskDelayUntil()` 会看到目标时间已经过去,它会立即返回而不实际延迟。

要解决这个问题:

`xLastWakeTime`需要在每次循环迭代中更新:
```c
xLastWakeTime = xTaskGetTickCount();
```
这会使延迟相对于当前的tick计数,提供实际的2个tick的延迟。

Tony607, 2023-07-31:
`xLastWakeTime`在`vTaskDelayUntil`中会自动更新，代码没有问题。

Closed 2023-07-31.

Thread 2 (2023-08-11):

原材料4010无刷电机的替代品

CiE-XinYuChen, 2023-08-11:
目前4010电机已经停产，市面上存货几乎耗尽且成本极高。请问作者有什么推荐的替代品？

Anthem86, 2024-03-04:
没找到，你们找到哪种替代品了

CiE-XinYuChen, 2024-03-11:
商家有一批铁氧体的尾货，扭矩降低了20%。。。我暂停了这个项目，不知道是否可行&nbsp;

XinYuChen
***@***.***

&nbsp;

------------------&nbsp;原始邮件&nbsp;------------------
发件人: ***@***.***&gt;;
发送时间: 2024年3月4日(星期一) 晚上9:26
收件人: ***@***.***&gt;;
抄送: ***@***.***&gt;; ***@***.***&gt;;
主题: Re: [Skythinker616/foc-wheel-legged-robot] 原材料4010无刷电机的替代品 (Issue #2)

没找到，你们找到哪种替代品了

—
Reply to this email directly, view it on GitHub, or unsubscribe.
You are receiving this because you authored the thread.Message ID: ***@***.***&gt;

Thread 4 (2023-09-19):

关于ctrl-proxy.py

tomhup, 2023-09-19:
在main函数中，采用了两个asyncio.run。导致两个函数串行执行，建议使用asyncio.gather 函数并行执行

Skythinker616, 2023-09-19:
程序设计的就是两个函数轮流执行，因为图传蓝牙需要作为主机连接控制板，又需要作为从机连接手机，经测试二者无法同时进行，程序会以“是否收到UDP数据”为准则在两种状态之间切换

Closed 2023-10-16.

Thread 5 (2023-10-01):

磁环

scybd, 2023-10-01:
请问2804电机的磁环要怎么配

chenhuiYu00, 2023-10-10:
> 请问2804电机的磁环要怎么配

我是用8mm外径磁环用502沾上去的

scybd, 2023-10-12:
我是买了个小点的磁环＋打印件，刚刚想起来打印件还没付款．．．待我试试

chenhuiYu00, 2023-10-12:
> 我是买了个小点的磁环＋打印件，刚刚想起来打印件还没付款．．．待我试试

这样也不错，到时候可以帮我看看你那里校准是什么个情况吗，我驱动电机校准一抖一抖，给电压指令也抖+发热，我找不到问题，难受

Skythinker616, 2023-10-16:
只要是跟随转子旋转的径向磁铁都可以，可以参考仓库说明中的选型，装配时我确实是用胶粘上的，热熔胶之类的都可以

scybd, 2023-10-21:
> > 我是买了个小点的磁环＋打印件，刚刚想起来打印件还没付款．．．待我试试
>
> 这样也不错，到时候可以帮我看看你那里校准是什么个情况吗，我驱动电机校准一抖一抖，给电压指令也抖+发热，我找不到问题，难受

我是新手，不懂怎么校准。
刚刚我才把驱动板焊好，试了一下开环跑12rad/s的转速，这电机过了20s左右就有点烫了，之后转个几秒会突然停止1秒左右继续转几秒然后停1秒，如此往复。不过倒是没有一抖一抖的。

chenhuiYu00, 2023-10-21:
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

这块驱动板怎么做到开环的😂，校准的话在手册了里面有说，长按按钮直到led灯常亮时松手就会触发校准

scybd, 2023-10-21:
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

开环的话就是单纯根据预设的速度和两次循环的间隔计算出$\theta$。
手册是这个电机的手册吗，淘宝客服说这是库存电机，没有资料。

chenhuiYu00, 2023-10-21:
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

这块驱动板作者在本项目里有相应的固件可以烧录，对三相电机是通用的。

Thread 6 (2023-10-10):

驱动板校准的电机发抖

chenhuiYu00, 2023-10-10:
驱动板校准的时候缓慢转了一会然后开始一卡一卡，之后发出开机的蜂鸣。当给电压指令后电机不旋转也是发抖一卡一卡，还发热。请问这个是什么问题？

Skythinker616, 2023-10-16:
可以检查一下硬件是否有虚焊问题导致驱动信号缺相，可以通过测量PWM引脚和输出引脚的波形进行判断

chenhuiYu00, 2023-10-21:
> 可以检查一下硬件是否有虚焊问题导致驱动信号缺相，可以通过测量PWM引脚和输出引脚的波形进行判断

我检查了硬件的虚焊，并用开环算法驱动电机按一定速度旋转，电机此时会正常旋转但会伴随着抖动（类似于高频振动）。我无法确定抖动是否是硬件上的原因，我焊接了四块驱动板都表现为该现象，请问我还可以排查什么方面的问题？

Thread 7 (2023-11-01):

请教控制程序中的两个参数

mailonghua, 2023-11-01:
void Motor_InitAll()
{
	Motor_Init(&leftJoint[0], 1.431, 7, 0.0316f, -1, Motor_CalcRevVolt4010);
	Motor_Init(&leftJoint[1], -7.76, 7, 0.0317f, 1, Motor_CalcRevVolt4010);
	Motor_Init(&leftWheel, 0, 4.0f, 0.0096f, 1, Motor_CalcRevVolt2804);
	Motor_Init(&rightJoint[0], 0.343, 7, 0.0299f, -1, Motor_CalcRevVolt4010);
	Motor_Init(&rightJoint[1], -2.446, 7, 0.0321f, -1, Motor_CalcRevVolt4010);
	Motor_Init(&rightWheel, 0, 4.0f, 0.0101f, 1, Motor_CalcRevVolt2804);
	xTaskCreate(Motor_SendTask, "Motor_SendTask", 2048, NULL, 5, NULL);
}
你好，想请问两个问题
1.torqueRatio参数是如何计算得到的？
2.反电动势的函数是根据什么计算出来的呢？

mailonghua, 2023-11-06:
有伙伴吗清楚吗？帮忙解答一下

DrinkingHook, 2023-11-08:
torqueRatio:电机的转矩比例系数,用于计算电压=扭矩/比例系数，每个电机型号都不一样,需要查datasheet获取

DrinkingHook, 2023-11-08:
> torqueRatio:电机的转矩比例系数,用于计算电压=扭矩/比例系数，每个电机型号都不一样,需要查datasheet获取

> 有伙伴吗清楚吗？帮忙解答一下

这个是al回答的，话说你做到哪一步了啊可以指导一下我吗

mailonghua, 2023-11-17:
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

目前是在重新设计轮足，包含硬件、软件、结构，目前还在调试电机驱动，随时交流

Skythinker616, 2023-11-21:
在`esp32-controller/README.md`中更新了对这些问题的解释

Skythinker616, 2023-11-23:
> 使用扭矩测量仪得到了不同电压下的堵转扭矩吗？

我用缠线+拉力计的简易方法测的，能有专用设备的话当然更好

Zhangyucong0210, 2023-11-23:
感谢回复，刚才就在看淘宝，发现扭矩仪太贵了，用拉力计感觉是最平民的方法
&nbsp;

张聿璁
***@***.***

&nbsp;

------------------&nbsp;原始邮件&nbsp;------------------
发件人: ***@***.***&gt;;
发送时间: 2023年11月23日(星期四) 晚上8:49
收件人: ***@***.***&gt;;
抄送: ***@***.***&gt;; ***@***.***&gt;;
主题: Re: [Skythinker616/foc-wheel-legged-robot] 请教控制程序中的两个参数 (Issue #7)

使用扭矩测量仪得到了不同电压下的堵转扭矩吗？

我用缠线+拉力计的简易方法测的，能有专用设备的话当然更好

—
Reply to this email directly, view it on GitHub, or unsubscribe.
You are receiving this because you commented.Message ID: ***@***.***&gt;

mailonghua, 2023-11-25:
> > 使用扭矩测量仪得到了不同电压下的堵转扭矩吗？
>
> 我用缠线+拉力计的简易方法测的，能有专用设备的话当然更好

1.电机厂家参数中提供了一个最大的扭矩，这个参数与堵转扭矩有什么关系，可以直接使用吗？除了上面提到方法还有其他的方式吗？
2.另外作者有没有考虑使用电流闭环，当前应该是使用了电压环路控制，两者你有什么建议吗

Zhangyucong0210, 2023-12-09:
> > 使用扭矩测量仪得到了不同电压下的堵转扭矩吗？
>
> 我用缠线+拉力计的简易方法测的，能有专用设备的话当然更好

你好，这个拉力计的安装位置是大腿打印件4颗螺丝的位置吗，我现在手边有拉力计，最大量程20N，但不确定力臂的长度应该是多少

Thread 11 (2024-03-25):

关于反电动势函数的建立与测量

Zhangyucong0210, 2024-03-25:
在readme中提到“测量反电动势时，给电机不同的电压，测量其空载转速，拟合为三次幂函数”。想请教下具体流程。
个人理解如下：
1.修改电机的目标电压，即FOC中力矩环的目标电压，得到电压v
2.读取电机现在的转速（rad/s）
3.重复以上步骤得到转速-电压的函数，修正到代码中

以上步骤是否有错误？并且我发现原函数并没有零次项，但我使用EXCEL散点图多项式拟合时，是存在零次项，该项是故意舍去还是使用其他方法拟合的结果？

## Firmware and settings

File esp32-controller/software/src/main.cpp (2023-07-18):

/* main.c
 * 主代码文件，包含所有主要代码逻辑
 * by L.B.W 2023
 * */

#include <Arduino.h>
#include <PID.h>
#include "driver/twai.h"
#include "I2Cdev.h"
#include "MPU6050_6Axis_MotionApps20.h"
#include "leg_pos.h"
#include "lqr_k.h"
#include "leg_conv.h"
#include "leg_spd.h"
#include <BLEDevice.h>
#include <BLEServer.h>
#include <BLE2902.h>
#include <esp_task_wdt.h>
#include <string.h>
#include <debug.h>

/*******************宏定义*******************/

//蓝牙各UUID及设备名称
#define UUID_SERVICE "4c9a0001-fb2e-432e-92ec-c6f5316b4689" //服务UUID
#define UUID_RX_CHARA "4c9a0002-fb2e-432e-92ec-c6f5316b4689" //接收特征UUID
#define UUID_TX_CHARA "4c9a0003-fb2e-432e-92ec-c6f5316b4689" //发送特征UUID
#define BLE_NAME "BalanceBot"

//计时工具，计算运行周期或经过时间
uint32_t timeCnt[6] = {0}, lastTimeCnt[6] = {0}, passTimeCnt[6] = {0};
#define TIME_COUNTER(num) do{timeCnt[num] = micros()-lastTimeCnt[num]; lastTimeCnt[num] = micros();}while(0)
#define PASS_TIME_START(num) uint32_t passTimeStart##num = micros()
#define PASS_TIME_STOP(num) passTimeCnt[num] = micros() - passTimeStart##num

/*******************结构体类型和全局变量定义*******************/

//IMU对象及数据
MPU6050 mpu;
struct IMUData
{
	float yaw, pitch, roll;			 // rad
	float yawSpd, pitchSpd, rollSpd; // rad/s
	float zAccel; // m/s^2
} imuData;

//电机结构体
//leftJoint[0]:左前关节电机, leftJoint[1]:左后关节电机, leftWheel:左车轮电机
//rightJoint[0]:右前关节电机, rightJoint[1]:右后关节电机, rightWheel:右车轮电机
struct Motor
{
	float speed;			   // rad/s
	float angle, offsetAngle;  // rad
	float voltage, maxVoltage; // V
	float torque, torqueRatio; // Nm, voltage = torque / torqueRatio
	float dir;				   // 1 or -1
	float (*calcRevVolt)(float speed); // 指向反电动势计算函数
} leftJoint[2], rightJoint[2], leftWheel, rightWheel; //六个电机对象

//腿部姿态结构体
struct LegPos
{
	float angle, length;   // rad, m
	float dAngle, dLength; // rad/s, m/s
	float ddLength;		   // m/s^2
} leftLegPos, rightLegPos; //左右腿部姿态

//状态变量结构体
struct StateVar
{
	float theta, dTheta;
	float x, dx;
	float phi, dPhi;
} stateVar;

//目标量结构体
struct Target
{
	float position;	 // m
	float speedCmd;	 // m/s
	float speed;    // m/s
	float yawSpeedCmd; // rad/s
	float yawAngle;	 // rad
	float rollAngle; // rad
	float legLength; // m
} target = {0, 0, 0, 0, 0, 0, 0.07f};

//触地检测数据结构体
struct GroundDetector
{
	float leftSupportForce, rightSupportForce;
	bool isTouchingGround, isCuchioning;
} groundDetector = {10, 10, true, false};

//站立过程状态枚举量
enum StandupState {
	StandupState_None,
	StandupState_Prepare,
	StandupState_Standup,
} standupState = StandupState_None;

CascadePID legAnglePID, legLengthPID; //腿部角度和长度控制PID
CascadePID yawPID, rollPID; //机身yaw和roll控制PID

//蓝牙相关全局对象指针
BLECharacteristic *chara_tx, *chara_rx;
BLEServer *server;
BLEService *service;

float motorOutRatio = 1.0f; //电机输出电压比例，对所有电机同时有效
float sourceVoltage = 12; //当前电源电压

/*******************函数声明*******************/

void setup();
void loop();

void Motor_Init(Motor *motor, float offsetAngle, float maxVoltage, float torqueRatio, float dir);
float Motor_CalcRevVolt4010(float speed);
float Motor_CalcRevVolt2804(float speed);
void Motor_InitAll();
void Motor_Update(Motor *motor, uint8_t *data);
void Motor_SetTorque(Motor *motor, float torque);
void Motor_UpdateVoltage(Motor *motor);
void Motor_SendTask(void *arg);

void CAN_RecvCallback(uint32_t id, uint8_t *data);
void CAN_RecvTask(void *arg);
void CAN_Init();
void CAN_SendFrame(uint32_t id, uint8_t *data);

void IMU_Task(void *arg);
void IMU_Init();

void Ctrl_TargetUpdateTask(void *arg);
void LegPos_UpdateTask(void *arg);
void Ctrl_StandupPrepareTask(void *arg);
void Ctrl_Task(void *arg);
void Ctrl_Init();

void BT_SendSampleTask(void *arg);
void BT_Init();

void Serial_Task(void *pvParameters);
void Serial_Init();

void ADC_Task(void *pvParameters);
void ADC_Init();

/*******************各模块函数定义*******************/

/******* 电机模块 *******/

//初始化一个电机对象
void Motor_Init(Motor *motor, float offsetAngle, float maxVoltage, float torqueRatio, float dir, float (*calcRevVolt)(float speed))
{
	motor->speed = motor->angle = motor->voltage = 0;
	motor->offsetAngle = offsetAngle;
	motor->maxVoltage = maxVoltage;
	motor->torqueRatio = torqueRatio;
	motor->dir = dir;
	motor->calcRevVolt = calcRevVolt;
}

//4010电机反电动势计算函数(输入速度，输出反电动势)
//测量并拟合出不同电压下对应的电机空载转速，调换自变量和因变量就是本函数
//由于该测量方法忽略阻力对空载转速的影响，最终抵消反电动势时也会抵消大部分电机本身的阻力
float Motor_CalcRevVolt4010(float speed)
{
	return 0.00008f * speed * speed * speed - 0.0035f * speed * speed + 0.2322f * speed;
}

//2804电机反电动势计算函数(输入速度，输出反电动势)，测量方法同上
float Motor_CalcRevVolt2804(float speed)
{
	return 0.000004f * speed * speed * speed - 0.0003f * speed * speed + 0.0266f * speed;
}

//初始化所有电机对象
//各个参数需要通过实际测量或拟合得到
void Motor_InitAll()
{
	Motor_Init(&leftJoint[0], 1.431, 7, 0.0316f, -1, Motor_CalcRevVolt4010);
	Motor_Init(&leftJoint[1], -7.76, 7, 0.0317f, 1, Motor_CalcRevVolt4010);
	Motor_Init(&leftWheel, 0, 4.0f, 0.0096f, 1, Motor_CalcRevVolt2804);
	Motor_Init(&rightJoint[0], 0.343, 7, 0.0299f, -1, Motor_CalcRevVolt4010);
	Motor_Init(&rightJoint[1], -2.446, 7, 0.0321f, -1, Motor_CalcRevVolt4010);
	Motor_Init(&rightWheel, 0, 4.0f, 0.0101f, 1, Motor_CalcRevVolt2804);
	xTaskCreate(Motor_SendTask, "Motor_SendTask", 2048, NULL, 5, NULL);
}

//从CAN总线接收到的数据中解析出电机角度和速度
void Motor_Update(Motor *motor, uint8_t *data)
{
	motor->angle = (*(int32_t *)&data[0] / 1000.0f - motor->offsetAngle) * motor->dir;
	motor->speed = (*(int16_t *)&data[4] / 10 * 2 * M_PI / 60) * motor->dir;
}

//设置电机扭矩
void Motor_SetTorque(Motor *motor, float torque)
{
	motor->torque = torque;
}

//由设置的目标扭矩和当前转速计算补偿反电动势后的驱动输出电压，并进行限幅
//补偿的意义: 电机转速越快反电动势越大，需要加大驱动电压来抵消反电动势，使电流(扭矩)不随转速发生变化
void Motor_UpdateVoltage(Motor *motor)
{
	float voltage = motor->torque / motor->torqueRatio * motorOutRatio;
	if (motor->speed >= 0)
		voltage += motor->calcRevVolt(motor->speed);
	else if (motor->speed < 0)
		voltage -= motor->calcRevVolt(-motor->speed);
	if (voltage > motor->maxVoltage)
		voltage = motor->maxVoltage;
	else if (voltage < -motor->maxVoltage)
		voltage = -motor->maxVoltage;
	motor->voltage = voltage * motor->dir;
}

//电机指令发送任务
void Motor_SendTask(void *arg)
{
	uint8_t data[8] = {0};
	Motor* motorList[] = {&leftJoint[0], &leftJoint[1], &leftWheel, &rightJoint[0], &rightJoint[1], &rightWheel};
	while (1)
	{
		for (int i = 0; i < 6; i++)
			Motor_UpdateVoltage(motorList[i]); //计算补偿后的电机电压
		
		*(int16_t *)&data[0] = ((int16_t)(leftJoint[0].voltage * 1000));
		*(int16_t *)&data[2] = ((int16_t)(leftJoint[1].voltage * 1000));
		*(int16_t *)&data[4] = ((int16_t)(leftWheel.voltage * 1000));
		CAN_SendFrame(0x100, data);
		*(int16_t *)&data[0] = ((int16_t)(rightJoint[0].voltage * 1000));
		*(int16_t *)&data[2] = ((int16_t)(rightJoint[1].voltage * 1000));
		*(int16_t *)&data[4] = ((int16_t)(rightWheel.voltage * 1000));
		CAN_SendFrame(0x200, data);
		vTaskDelay(2);
	}
}

/******* CAN通信模块 *******/

//CAN收到数据后进入的回调函数
void CAN_RecvCallback(uint32_t id, uint8_t *data)
{
	switch (id) //根据CAN ID更新各电机数据
	{
	case 0x101:
		Motor_Update(&leftJoint[0], data);
		break;
	case 0x102:
		Motor_Update(&leftJoint[1], data);
		break;
	case 0x103:
		Motor_Update(&leftWheel, data);
		break;
	case 0x105:
		Motor_Update(&rightJoint[0], data);
		break;
	case 0x106:
		Motor_Update(&rightJoint[1], data);
		break;
	case 0x107:
		Motor_Update(&rightWheel, data);
		break;
	}
}

//CAN数据帧轮询接收任务
void CAN_RecvTask(void *arg)
{
	twai_message_t msg;
	twai_status_info_t status;
	
	TickType_t xLastWakeTime = xTaskGetTickCount();
	while (1)
	{
		twai_get_status_info(&status);
		for(uint8_t i = 0; i < status.msgs_to_rx; i++)
		{
			if(twai_receive(&msg, 0) == ESP_OK)
				CAN_RecvCallback(msg.identifier, msg.data);
		}
		vTaskDelayUntil(&xLastWakeTime, 2); //2ms轮询一次
	}
}

//CAN通信外设初始化
void CAN_Init()
{
	twai_general_config_t twai_conf = {
		.mode = TWAI_MODE_NORMAL,
		.tx_io = GPIO_NUM_6,
		.rx_io = GPIO_NUM_7,
		.clkout_io = TWAI_IO_UNUSED,
		.bus_off_io = TWAI_IO_UNUSED,
		.tx_queue_len = 5,
		.rx_queue_len = 10,
		.alerts_enabled = TWAI_ALERT_NONE,
		.clkout_divider = 0,
		.intr_flags = ESP_INTR_FLAG_LEVEL1};

	twai_timing_config_t twai_timing = TWAI_TIMING_CONFIG_1MBITS();

	twai_filter_config_t twai_filter = {
		.acceptance_code = 0x00000000,
		.acceptance_mask = 0xFFFFFFFF,
		.single_filter = true};

	twai_driver_install(&twai_conf, &twai_timing, &twai_filter);
	twai_start();
	xTaskCreate(CAN_RecvTask, "CAN_RecvTask", 2048, NULL, 5, NULL);
}

//发送一帧CAN数据(data为8字节数据)
void CAN_SendFrame(uint32_t id, uint8_t *data)
{
	twai_message_t msg;
	msg.flags = 0;
	msg.identifier = id;
	msg.data_length_code = 8;
	memcpy(msg.data, data, 8);
	twai_transmit(&msg, 100);
}

/******* 陀螺仪模块 *******/

//陀螺仪数据获取任务
void IMU_Task(void *arg)
{
	TickType_t xLastWakeTime = xTaskGetTickCount();

	uint8_t fifoBuffer[64]; //dmp数据接收区
	int16_t yawRound = 0; //统计yaw转过的整圈数
	float lastYaw = 0;
	
	while (1)
	{
		if (mpu.dmpGetCurrentFIFOPacket(fifoBuffer))
		{
			//获取陀螺仪角速度
			int16_t gyroData[3];
			mpu.getRotation(&gyroData[0], &gyroData[1], &gyroData[2]);
			imuData.rollSpd = gyroData[1] / 16.4f * M_PI / 180.0f;
			imuData.pitchSpd = -gyroData[0] / 16.4f * M_PI / 180.0f;
			imuData.yawSpd = gyroData[2] / 16.4f * M_PI / 180.0f;
			
			//获取陀螺仪欧拉角
			float ypr[3];
			Quaternion q;
			VectorFloat gravity;
			mpu.dmpGetQuaternion(&q, fifoBuffer);
			mpu.dmpGetGravity(&gravity, &q);
			mpu.dmpGetYawPitchRoll(ypr, &q, &gravity);
			float yaw = -ypr[0];
			imuData.pitch = -ypr[2];
			imuData.roll = -ypr[1];

			if (yaw - lastYaw > M_PI)
				yawRound--;
			else if (yaw - lastYaw < -M_PI)
				yawRound++;
			lastYaw = yaw;
			imuData.yaw = yaw + yawRound * 2 * M_PI; //imuData.yaw为累计转角

			//获取陀螺仪Z轴加速度
			VectorInt16 rawAccel;
			mpu.dmpGetAccel(&rawAccel, fifoBuffer);
			VectorInt16 accel;
			mpu.dmpGetLinearAccel(&accel, &rawAccel, &gravity);
			imuData.zAccel = accel.z / 8192.0f * 9.8f;
		}
		vTaskDelayUntil(&xLastWakeTime, 5); //5ms轮询一次
	}
}

//陀螺仪模块初始化
void IMU_Init()
{
	//初始化IIC
	Wire.begin(5, 4);
	Wire.setClock(400000);

	//初始化陀螺仪
	mpu.initialize();
	Serial.println(mpu.testConnection() ? "MPU6050 connection successful" : "MPU6050 connection failed");
	Serial.println("Address: 0x" + String(mpu.getDeviceID(), HEX));
	mpu.setFullScaleAccelRange(MPU6050_IMU::MPU6050_ACCEL_FS_16);
	while(mpu.dmpInitialize() != 0);
	mpu.setXAccelOffset(-668);
	mpu.setYAccelOffset(-1632);
	mpu.setZAccelOffset(998);
	mpu.setXGyroOffset(283);
	mpu.setYGyroOffset(80);
	mpu.setZGyroOffset(42);
	// mpu.CalibrateAccel(6); //测量偏移数据
	// mpu.CalibrateGyro(6);
	// mpu.PrintActiveOffsets();
	mpu.setDMPEnabled(true);

	//开启陀螺仪数据获取任务
	xTaskCreate(IMU_Task, "IMU_Task", 2048, NULL, 5, NULL);
}

/******* 运动控制模块 *******/

//目标量更新任务(根据蓝牙收到的目标量计算实际控制算法的给定量)
void Ctrl_TargetUpdateTask(void *arg)
{
	TickType_t xLastWakeTime = xTaskGetTickCount();
	float speedSlopeStep = 0.003f;
	while (1)
	{
		//根据当前腿长计算速度斜坡步长(腿越短越稳定，加减速斜率越大)
		float legLength = (leftLegPos.length + rightLegPos.length) / 2;
		speedSlopeStep = -(legLength - 0.07f) * 0.02f + 0.002f;

		//计算速度斜坡，斜坡值更新到target.speed
		if(fabs(target.speedCmd - target.speed) < speedSlopeStep)
			target.speed = target.speedCmd;
		else
		{
			if(target.speedCmd - target.speed > 0)
				target.speed += speedSlopeStep;
			else
				target.speed -= speedSlopeStep;
		}

		//计算位置目标，并限制在当前位置的±0.1m内
		target.position += target.speed * 0.004f;
		if(target.position - stateVar.x > 0.1f)
			target.position = stateVar.x + 0.1f; 
		else if(target.position - stateVar.x < -0.1f)
			target.position = stateVar.x - 0.1f;

		//限制速度目标在当前速度的±0.3m/s内
		if(target.speed - stateVar.dx > 0.3f)
			target.speed = stateVar.dx + 0.3f;
		else if(target.speed - stateVar.dx < -0.3f)
			target.speed = stateVar.dx - 0.3f;

		//计算yaw方位角目标
		target.yawAngle += target.yawSpeedCmd * 0.004f;
		
		vTaskDelayUntil(&xLastWakeTime, 4); //每4ms更新一次
	}
}

//腿部姿态更新任务(根据关节电机数据计算腿部姿态)
void LegPos_UpdateTask(void *arg)
{
	const float lpfRatio = 0.5f; //低通滤波系数(新值的权重)
	float lastLeftDLength = 0, lastRightDLength = 0;
	TickType_t xLastWakeTime = xTaskGetTickCount();
	while (1)
	{
		float legPos[2], legSpd[2];

		//计算左腿位置
		leg_pos(leftJoint[1].angle, leftJoint[0].angle, legPos);
		leftLegPos.length = legPos[0];
		leftLegPos.angle = legPos[1];

		//计算左腿速度
		leg_spd(leftJoint[1].speed, leftJoint[0].speed, leftJoint[1].angle, leftJoint[0].angle, legSpd);
		leftLegPos.dLength = legSpd[0];
		leftLegPos.dAngle = legSpd[1];

		//计算左腿腿长加速度
		leftLegPos.ddLength = ((leftLegPos.dLength - lastLeftDLength) * 1000 / 4) * lpfRatio + leftLegPos.ddLength * (1 - lpfRatio);
		lastLeftDLength = leftLegPos.dLength;

		//计算右腿位置
		leg_pos(rightJoint[1].angle, rightJoint[0].angle, legPos);
		rightLegPos.length = legPos[0];
		rightLegPos.angle = legPos[1];

		//计算右腿速度
		leg_spd(rightJoint[1].speed, rightJoint[0].speed, rightJoint[1].angle, rightJoint[0].angle, legSpd);
		rightLegPos.dLength = legSpd[0];
		rightLegPos.dAngle = legSpd[1];

		//计算右腿腿长加速度
		rightLegPos.ddLength = ((rightLegPos.dLength - lastRightDLength) * 1000 / 4) * lpfRatio + rightLegPos.ddLength * (1 - lpfRatio);
		lastRightDLength = rightLegPos.dLength;

		vTaskDelayUntil(&xLastWakeTime, 4); //每4ms更新一次
	}
}

//站立准备任务(将机器人从任意姿态调整到准备站立前的劈叉状态)
void Ctrl_StandupPrepareTask(void *arg)
{
	standupState = StandupState_Prepare;

	//将左腿向后摆
	Motor_SetTorque(&leftJoint[0], 0.2f);
	Motor_SetTorque(&leftJoint[1], 0.2f);
	while(leftLegPos.angle < M_3PI_4)
		vTaskDelay(5);
	Motor_SetTorque(&leftJoint[0], 0);
	Motor_SetTorque(&leftJoint[1], 0);
	vTaskDelay(1000);

	//将右腿向前摆
	Motor_SetTorque(&rightJoint[0], -0.2f);
	Motor_SetTorque(&rightJoint[1], -0.2f);
	while(rightLegPos.angle > M_PI_4)
		vTaskDelay(5);
	Motor_SetTorque(&rightJoint[0], 0);
	Motor_SetTorque(&rightJoint[1], 0);
	vTaskDelay(1000);

	//完成准备动作，关闭电机结束任务
	Motor_SetTorque(&leftJoint[0], 0);
	Motor_SetTorque(&leftJoint[1], 0);
	Motor_SetTorque(&leftWheel, 0);
	Motor_SetTorque(&rightJoint[0], 0);
	Motor_SetTorque(&rightJoint[1], 0);
	Motor_SetTorque(&rightWheel, 0);
	
	standupState = StandupState_Standup;

	vTaskDelete(NULL);
}

//主控制任务
void Ctrl_Task(void *arg)
{
	const float wheelRadius = 0.026f; //m，车轮半径
	const float legMass = 0.05f; //kg，腿部质量

	TickType_t xLastWakeTime = xTaskGetTickCount();

	//手动为反馈矩阵和输出叠加一个系数，用于手动优化控制效果
	float kRatio[2][6] = {{1.0f, 1.0f, 1.0f, 1.0f, 1.0f, 1.0f},
						{1.0f, 1.0f, 1.0f, 1.0f, 1.0f, 1.0f}};
	float lqrTpRatio = 1.0f, lqrTRatio = 1.0f;

	//设定初始目标值
	target.rollAngle = 0.0f;
	target.legLength = 0.07f;
	target.speed = 0.0f;
	target.position = (leftWheel.angle + rightWheel.angle) / 2 * wheelRadius;

	while (1)
	{
		//计算状态变量
		stateVar.phi = imuData.pitch;
		stateVar.dPhi = imuData.pitchSpd;
		stateVar.x = (leftWheel.angle + rightWheel.angle) / 2 * wheelRadius;
		stateVar.dx = (leftWheel.speed + rightWheel.speed) / 2 * wheelRadius;
		stateVar.theta = (leftLegPos.angle + rightLegPos.angle) / 2 - M_PI_2 - imuData.pitch;
		stateVar.dTheta = (leftLegPos.dAngle + rightLegPos.dAngle) / 2 - imuData.pitchSpd;
		float legLength = (leftLegPos.length + rightLegPos.length) / 2;
		float dLegLength = (leftLegPos.dLength + rightLegPos.dLength) / 2;

		//如果正在站立准备状态，则不进行后续控制
		if(standupState == StandupState_Prepare)
		{
			vTaskDelayUntil(&xLastWakeTime, 4);
			continue;
		}

		//计算LQR反馈矩阵
		float kRes[12] = {0}, k[2][6] = {0};
		lqr_k(legLength, kRes);
		if(groundDetector.isTouchingGround) //正常触地状态
		{
			for (int i = 0; i < 6; i++)
			{
				for (int j = 0; j < 2; j++)
					k[j][i] = kRes[i * 2 + j] * kRatio[j][i];
			}
		}
		else //腿部离地状态，手动修改反馈矩阵，仅保持腿部竖直
		{
			memset(k, 0, sizeof(k));
			k[1][0] = kRes[1] * -2;
			k[1][1] = kRes[3] * -10;
		}

		//准备状态变量
		float x[6] = {stateVar.theta, stateVar.dTheta, stateVar.x, stateVar.dx, stateVar.phi, stateVar.dPhi};
		//与给定量作差
		x[2] -= target.position;
		x[3] -= target.speed;

		//矩阵相乘，计算LQR输出
		float lqrOutT = k[0][0] * x[0] + k[0][1] * x[1] + k[0][2] * x[2] + k[0][3] * x[3] + k[0][4] * x[4] + k[0][5] * x[5];
		float lqrOutTp = k[1][0] * x[0] + k[1][1] * x[1] + k[1][2] * x[2] + k[1][3] * x[3] + k[1][4] * x[4] + k[1][5] * x[5];

		//计算yaw轴PID输出
		PID_CascadeCalc(&yawPID, target.yawAngle, imuData.yaw, imuData.yawSpd);
		
		//设定车轮电机输出扭矩，为LQR和yaw轴PID输出的叠加
		if(groundDetector.isTouchingGround) //正常接地状态
		{
			Motor_SetTorque(&leftWheel, -lqrOutT * lqrTRatio - yawPID.output);
			Motor_SetTorque(&rightWheel, -lqrOutT * lqrTRatio + yawPID.output);
		}
		else //腿部离地状态，关闭车轮电机
		{
			Motor_SetTorque(&leftWheel, 0);
			Motor_SetTorque(&rightWheel, 0);
		}

		//根据离地状态修改目标腿长，并计算腿长PID输出
		PID_CascadeCalc(&legLengthPID, (groundDetector.isTouchingGround && !groundDetector.isCuchioning) ? target.legLength : 0.12f, legLength, dLegLength);
		//计算roll轴PID输出
		PID_CascadeCalc(&rollPID, target.rollAngle, imuData.roll, imuData.rollSpd);
		//根据离地状态计算左右腿推力，若离地则不考虑roll轴PID输出和前馈量
		float leftForce = legLengthPID.output + ((groundDetector.isTouchingGround && !groundDetector.isCuchioning) ? 6-rollPID.output : 0);
		float rightForce = legLengthPID.output + ((groundDetector.isTouchingGround && !groundDetector.isCuchioning) ? 6+rollPID.output : 0);
		if(leftLegPos.length > 0.12f) //保护腿部不能伸太长
			leftForce -= (leftLegPos.length - 0.12f) * 100;
		if(rightLegPos.length > 0.12f)
			rightForce -= (rightLegPos.length - 0.12f) * 100;
		
		//计算左右腿的地面支持力
		groundDetector.leftSupportForce = leftForce + legMass * 9.8f - legMass * (leftLegPos.ddLength - imuData.zAccel);
		groundDetector.rightSupportForce = rightForce + legMass * 9.8f - legMass * (rightLegPos.ddLength - imuData.zAccel);
		//更新离地检测器数据
		static uint32_t lastTouchTime = 0;
		bool isTouchingGround = groundDetector.leftSupportForce > 3 && groundDetector.rightSupportForce > 3; //判断当前瞬间是否接地
		if(!isTouchingGround && millis() - lastTouchTime < 1000) //若上次触地时间距离现在不超过1s，则认为当前瞬间接地，避免弹跳导致误判
			isTouchingGround = true;
		if(!groundDetector.isTouchingGround && isTouchingGround) //判断转为接地状态，标记进入缓冲状态
		{
			target.position = stateVar.x;
			groundDetector.isCuchioning = true;
			lastTouchTime = millis();
		}
		if(groundDetector.isCuchioning && legLength < target.legLength) //缓冲状态直到腿长压缩到目标腿长结束
			groundDetector.isCuchioning = false;
		groundDetector.isTouchingGround = isTouchingGround;

		//计算左右腿角度差PID输出
		PID_CascadeCalc(&legAnglePID, 0, leftLegPos.angle - rightLegPos.angle, leftLegPos.dAngle - rightLegPos.dAngle);
		
		//计算髋关节扭矩输出，为LQR输出和左右腿角度差PID输出的叠加
		float leftTp = lqrOutTp * lqrTpRatio - legAnglePID.output * (leftLegPos.length / 0.07f);
		float rightTp = lqrOutTp * lqrTpRatio + legAnglePID.output * (rightLegPos.length / 0.07f);
		
		//使用VMC计算各关节电机输出扭矩
		float leftJointTorque[2]={0};
		leg_conv(leftForce, leftTp, leftJoint[1].angle, leftJoint[0].angle, leftJointTorque);
		float rightJointTorque[2]={0};
		leg_conv(rightForce, rightTp, rightJoint[1].angle, rightJoint[0].angle, rightJointTorque);
		
		//保护腿部角度不超限
		float leftTheta = leftLegPos.angle - imuData.pitch - M_PI_2;
		float rightTheta = rightLegPos.angle - imuData.pitch - M_PI_2;
		#define PROTECT_CONDITION (leftTheta < -M_PI_4 || leftTheta > M_PI_4 || \
								   rightTheta < -M_PI_4 || rightTheta > M_PI_4 || \
								   imuData.pitch > M_PI_4 || imuData.pitch < -M_PI_4) //腿部角度超限保护条件
		if(PROTECT_CONDITION) //当前达到保护条件
		{
			if(standupState == StandupState_None) //未处于起立过程中
			{
				//关闭所有电机
				Motor_SetTorque(&leftWheel, 0);
				Motor_SetTorque(&rightWheel, 0);
				Motor_SetTorque(&leftJoint[0], 0);
				Motor_SetTorque(&leftJoint[1], 0);
				Motor_SetTorque(&rightJoint[0], 0);
				Motor_SetTorque(&rightJoint[1], 0);
				//阻塞等待腿部角度回到安全范围，再等待4s后恢复控制(若中途触发了起立则在起立准备完成后直接跳出)
				while(PROTECT_CONDITION && standupState == StandupState_None)
				{
					leftTheta = leftLegPos.angle - imuData.pitch - M_PI_2;
					rightTheta = rightLegPos.angle - imuData.pitch - M_PI_2;
					vTaskDelay(100);
				}
				if(standupState == StandupState_None)
					vTaskDelay(4000);
				//退出保护后设定目标位置和yaw角度为当前值
				target.position = (leftWheel.angle + rightWheel.angle) / 2 * wheelRadius;
				target.yawAngle = imuData.yaw;
				continue;
			}
			if(standupState == StandupState_Standup && (leftTheta < -M_PI_4 || rightTheta > M_PI_4))
				standupState = StandupState_None;
		}
		else
		{
			if(standupState == StandupState_Standup) //未达到保护条件且处于起立过程中，说明起立完成，退出起立过程
				standupState = StandupState_None;
		}

		//设定关节电机输出扭矩
		Motor_SetTorque(&leftJoint[0], -leftJointTorque[0]);
		Motor_SetTorque(&leftJoint[1], -leftJointTorque[1]);
		Motor_SetTorque(&rightJoint[0], -rightJointTorque[0]);
		Motor_SetTorque(&rightJoint[1], -rightJointTorque[1]);

		vTaskDelayUntil(&xLastWakeTime, 4); //4ms控制周期
	}
}

//控制模块初始化
void Ctrl_Init()
{
	//初始化各个PID参数
	PID_Init(&yawPID.inner, 0.01, 0, 0, 0, 0.1);
	PID_Init(&yawPID.outer, 10, 0, 0, 0, 2);
	PID_Init(&rollPID.inner, 1, 0, 5, 0, 5);
	PID_Init(&rollPID.outer, 20, 0, 0, 0, 3);
	PID_SetErrLpfRatio(&rollPID.inner, 0.1f);
	PID_Init(&legLengthPID.inner, 10.0f, 1, 30.0f, 2.0f, 10.0f);
	PID_Init(&legLengthPID.outer, 5.0f, 0, 0.0f, 0.0f, 0.5f);
	PID_SetErrLpfRatio(&legLengthPID.inner, 0.5f);
	PID_Init(&legAnglePID.inner, 0.04, 0, 0, 0, 1);
	PID_Init(&legAnglePID.outer, 12, 0, 0, 0, 20);
	PID_SetErrLpfRatio(&legAnglePID.outer, 0.5f);

	//触发各个控制任务
	xTaskCreate(Ctrl_TargetUpdateTask, "Ctrl_TargetUpdateTask", 4096, NULL, 3, NULL);
	xTaskCreate(LegPos_UpdateTask, "LegPos_UpdateTask", 4096, NULL, 2, NULL);
	vTaskDelay(2);
	xTaskCreate(Ctrl_Task, "Ctrl_Task", 4096, NULL, 1, NULL);
}

/******* 蓝牙模块 *******/

//通过蓝牙notify发送数据
extern "C" void BT_Send(uint8_t *data, uint32_t len)
{
	chara_tx->setValue(data, len);
	chara_tx->notify();
}
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
extern "C" void app_main()
{
	setup();
	while (1)
	{
		loop();
	}
}

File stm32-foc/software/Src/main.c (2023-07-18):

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

/* Includes ------------------------------------------------------------------*/
#include "main.h"
#include "can.h"
#include "tim.h"
#include "gpio.h"

/* USER CODE BEGIN Includes */
#include <stdio.h>
#include <string.h>
#include "MagneticSensor.h" 
#include "FOCMotor.h"
#include "BLDCmotor.h"
#include "FlashStorage.h"
/* USER CODE END Includes */

/* USER CODE BEGIN PTD */

//用于蜂鸣的音符
enum
{
	//不响
	T_None=0,
	//低八度
  T_L1=3822,
  T_L2=3405,
  T_L3=3034,
  T_L4=2863,
  T_L5=2551,
  T_L6=2272,
  T_L7=2052,
	//中八度
  T_M1=1911,
  T_M2=1703,
  T_M3=1517,
  T_M4=1432,
  T_M5=1276,
  T_M6=1136,
  T_M7=1012,
	//高八度
  T_H1=956,
  T_H2=851,
  T_H3=758,
  T_H4=716,
  T_H5=638,
  T_H6=568,
  T_H7=506
};

//卡尔曼滤波结构体
typedef struct{
	float X_last;
	float X_mid;
	float X_now;
	float P_mid;
	float P_now;
	float P_last;
	float kg;
	float A;
	float Q;
	float R;
	float H;
} Kalman;
/* USER CODE END PTD */

/* USER CODE BEGIN PM */
#define VOLT_SUPPLY 12 //供电母线电压
#define MAX_VOLT 6.9f  //限制供电电压(平均值)，最高为VOLT_SUPPLY/√3; 4010电机:6.9V, 2804电机:4V
/* USER CODE END PM */


/* USER CODE BEGIN PV */
float targetVotage = 0;    //当前目标电压
uint8_t beepPlaying = 0;   //当前是否在蜂鸣状态
uint8_t motorID = 1;       //初始电机ID
uint8_t ledBlink = 1;      //led是否处于正常闪烁模式
float speed = 0;           //传感器作差数据所得转速
float filteredAngle = 0;   //经滤波得到的转子角度
uint32_t lastRecvTime = 0; //上次收到CAN数据帧的时间
Kalman angleFilter; //卡尔曼滤波结构体
/* USER CODE END PV */

void SystemClock_Config(void);
/* USER CODE BEGIN 0 */
int fputc(int ch, FILE *f) { return ch; }

//单片机软件复位
void System_Reset(void)
{
	__set_FAULTMASK(1);
	NVIC_SystemReset();
}

/*************卡尔曼滤波*************/

void Kalman_Init(Kalman* p,float T_Q,float T_R)
{
	p->X_last = (float)0;
	p->P_last = 0;
	p->Q = T_Q;
	p->R = T_R;
	p->A = 1;
	p->H = 1;
	p->X_mid = p->X_last;
}

float Kalman_Filter(Kalman* p,float dat)
{
	if(!p) return 0;
	p->X_mid =p->A*p->X_last;                     //x(k|k-1) = AX(k-1|k-1)+BU(k)
	p->P_mid = p->A*p->P_last+p->Q;               //p(k|k-1) = Ap(k-1|k-1)A'+Q
	p->kg = p->P_mid/(p->P_mid+p->R);             //kg(k) = p(k|k-1)H'/(Hp(k|k-1)'+R)
	p->X_now = p->X_mid+p->kg*(dat-p->X_mid);     //x(k|k) = X(k|k-1)+kg(k)(Z(k)-HX(k|k-1))
	p->P_now = (1-p->kg)*p->P_mid;                //p(k|k) = (I-kg(k)H)P(k|k-1)
	p->P_last = p->P_now;
	p->X_last = p->X_now;
	return p->X_now;
}

/*************CAN通信*************/

//CAN外设初始化
void CAN_Init()
{
	CAN_FilterTypeDef filter;
	filter.FilterActivation = ENABLE;
	filter.FilterMode = CAN_FILTERMODE_IDMASK;
	filter.FilterMode = CAN_FILTERMODE_IDMASK;
	filter.FilterScale = CAN_FILTERSCALE_32BIT;
	filter.FilterIdHigh = 0x0000;
	filter.FilterIdLow = 0x0000;
	filter.FilterMaskIdHigh = 0x0000;
	filter.FilterMaskIdLow = 0x0000;
	filter.FilterBank = 0;
	filter.FilterFIFOAssignment = CAN_RX_FIFO0;
	HAL_CAN_ConfigFilter(&hcan, &filter);
	HAL_CAN_Start(&hcan);
	HAL_CAN_ActivateNotification(&hcan, CAN_IT_RX_FIFO0_MSG_PENDING);
}

//发送一个反馈数据帧
void CAN_SendState(float angle, float speed)
{
	CAN_TxHeaderTypeDef header;
	header.StdId = motorID + 0x100;
	header.IDE = CAN_ID_STD;
	header.RTR = CAN_RTR_DATA;
	header.DLC = 8;
	
	uint8_t data[8];
	memcpy(data,&(int32_t){angle*1000},4); //角度数据放在前四个字节
	memcpy(&data[4],&(int16_t){speed*10},2); //转速数据放在第5-6字节
	
	uint32_t mailbox;
	HAL_CAN_AddTxMessage(&hcan, &header, data, &mailbox);
}

//CAN收到数据的中断回调
void HAL_CAN_RxFifo0MsgPendingCallback(CAN_HandleTypeDef *hcan)
{
	CAN_RxHeaderTypeDef header;
	uint8_t rxData[8];
	
	if(HAL_CAN_GetRxMessage(hcan, CAN_RX_FIFO0, &header, rxData) != HAL_OK)
		return;
	
	if(header.StdId == 0x100 && motorID <= 4) //ID=1~4接收0x100数据帧
	{
		targetVotage = *(int16_t*)&rxData[(motorID-1)*2] / 1000.0f;
		lastRecvTime = HAL_GetTick();
	}
	else if(header.StdId == 0x200 && motorID > 4) //ID=5~8接收0x200数据帧
	{
		targetVotage = *(int16_t*)&rxData[(motorID-5)*2] / 1000.0f;
		lastRecvTime = HAL_GetTick();
	}
}

/*************FOC*************/

void SimpleFOC_Init()
{
	HAL_TIM_PWM_Start(&htim2,TIM_CHANNEL_1); //开启三个PWM通道输出
	HAL_TIM_PWM_Start(&htim2,TIM_CHANNEL_2);
	HAL_TIM_PWM_Start(&htim2,TIM_CHANNEL_3);
	
	MagneticSensor_Init(); //初始化磁传感器
	
	voltage_power_supply=VOLT_SUPPLY; //设定FOC所需参数
	voltage_limit=MAX_VOLT;
	voltage_sensor_align=voltage_limit;
	targetVotage=0;
	
	Motor_init(); //初始化电机信息
	Motor_initFOC(); //初始化FOC参数
	
	motorID = Flash_ReadMotorID(); //从Flash读取电机ID
	motorID = motorID ? motorID : 1;
}

/*************蜂鸣*************/

//根据蜂鸣周期配置并触发定时器
void Beep_Play(uint16_t period)
{
	if(period!=0)
	{
		__HAL_TIM_SetAutoreload(&htim1,period/2);
		HAL_TIM_Base_Start_IT(&htim1);
		beepPlaying = 1;
	}
	else
	{
		HAL_TIM_Base_Stop_IT(&htim1);
		beepPlaying = 0;
	}
}

//播放一串音符
void Beep_PlayNotes(uint8_t num, uint16_t notes[][2])
{
	for(uint8_t i=0; i<num; i++)
	{
		Beep_Play(notes[i][0]);
		HAL_Delay(notes[i][1]);
	}
	Beep_Play(0);
}

//蜂鸣中断处理，在定时器中断回调中调用
void Beep_IRQHandler()
{
	static uint8_t flipFlag = 0;
	if(targetVotage == 0)
	{
		setPhaseVoltage(voltage_limit/2, 0, _PI/3 * flipFlag); //使磁场方向在0-PI/3间震荡
		flipFlag = !flipFlag;
	}
}

/*************各个定时任务*************/

//非阻塞按键处理
void Key_Process()
{
	static uint32_t downTime = 0;
	static uint8_t lastKeyState = 0;
	uint8_t keyState = (HAL_GPIO_ReadPin(GPIOA, GPIO_PIN_3) == GPIO_PIN_RESET) ? 1 : 0;
	if(keyState && !lastKeyState) //按下
	{
		downTime = HAL_GetTick();
		ledBlink = 0;
	}
	else if(keyState && lastKeyState) //按住
	{
		uint32_t pressTime = HAL_GetTick() - downTime;
		if(pressTime < 500*8) //闪8下，每次500ms
		{
			if(pressTime%500 < 100)
				HAL_GPIO_WritePin(GPIOC, GPIO_PIN_13, GPIO_PIN_SET);
			else
				HAL_GPIO_WritePin(GPIOC, GPIO_PIN_13, GPIO_PIN_RESET);
		}
		else if(pressTime < 500*12)
			HAL_GPIO_WritePin(GPIOC, GPIO_PIN_13, GPIO_PIN_SET);
		else
			HAL_GPIO_WritePin(GPIOC, GPIO_PIN_13, GPIO_PIN_RESET); //闪8下之后常亮
	}
	else if(!keyState && lastKeyState) //松开
	{
		uint32_t pressTime = HAL_GetTick() - downTime;
		if(pressTime > 50 && pressTime <500*8) //闪8下以内松开，设置ID
		{
			motorID = pressTime/500 + 1;
			Flash_SaveMotorID(motorID);
		}
		else if(pressTime >= 500*8 && pressTime < 500*12) //闪8下后松开，清空Flash后复位重新校准
		{
			Flash_EraseMotorParam();
			System_Reset();
		}
		HAL_GPIO_WritePin(GPIOC, GPIO_PIN_13, GPIO_PIN_RESET);
		ledBlink = 1;
	}
	lastKeyState = keyState;
}

//非阻塞LED定时任务，闪烁次数表示电机ID
void Led_Process()
{
	if(!ledBlink) return;
	uint32_t period = 1000 + (100+200)*motorID;
	uint32_t mod = HAL_GetTick() % period;
	if(mod < (100+200)*motorID && mod%(100+200) < 100)
		HAL_GPIO_WritePin(GPIOC, GPIO_PIN_13, GPIO_PIN_SET);
	else
		HAL_GPIO_WritePin(GPIOC, GPIO_PIN_13, GPIO_PIN_RESET);
}

//电机转速计算
void Motor_SpeedCalcProcess()
{
	const uint8_t speedLpfLen = 5;
	static float speedLpfBuf[speedLpfLen] = {0}; //存放5个filteredAngle
	
	float angle = filteredAngle;
	float curSpeed = (angle-speedLpfBuf[0])*1000/speedLpfLen/_2PI*60;
	speed = curSpeed;
	
	for(uint8_t i=0; i<speedLpfLen-1; i++)
		speedLpfBuf[i] = speedLpfBuf[i+1];
	speedLpfBuf[speedLpfLen-1] = angle;
}
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

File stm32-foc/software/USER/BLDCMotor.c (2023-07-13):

/************************************************
本文件主要来自CSDN博主loop222对SimpleFOC项目的移植
原教程：https://blog.csdn.net/loop222/article/details/120471390
本项目删除了部分代码，添加了Flash数据读取和对蜂鸣功能的兼容
************************************************/

#include "BLDCmotor.h"
#include "FOCMotor.h"
#include "foc_utils.h"
#include "gpio.h"
#include <stdio.h>
#include "MagneticSensor.h" 
#include "tim.h"
#include "FlashStorage.h"

#define M1_Enable HAL_GPIO_WritePin(GPIOA,GPIO_PIN_4,GPIO_PIN_SET)
#define M1_Disable HAL_GPIO_WritePin(GPIOA,GPIO_PIN_4,GPIO_PIN_RESET)
#define PWM_Period 1280

extern float target;

long sensor_direction;
float voltage_power_supply;
float voltage_limit;
float voltage_sensor_align;
int  pole_pairs;
unsigned long open_loop_timestamp;
float velocity_limit;

int alignSensor(void);
float velocityOpenloop(float target_velocity);
float angleOpenloop(float target_angle);
/******************************************************************************/
void Motor_init(void)
{
	printf("MOT: Init\r\n");
	
	if(voltage_sensor_align > voltage_limit)
		voltage_sensor_align = voltage_limit;
	
	pole_pairs=7;
	sensor_direction=UNKNOWN;
	M1_Enable;
	printf("MOT: Enable driver.\r\n");
}
/******************************************************************************/
void Motor_initFOC(void)
{
	if(Flash_ReadMotorParam(&pole_pairs, &zero_electric_angle, (int*)&sensor_direction) == -1) //尝试读取Flash数据
	{
		if(alignSensor()) //读取识别则进行电机校准，检测零点偏移量和极对数
			Flash_SaveMotorParam(pole_pairs, zero_electric_angle, sensor_direction); //校准数据存入Flash
	}
	
	//added the shaft_angle update
	angle_prev=getAngle();  //getVelocity(),make sure velocity=0 after power on
	HAL_Delay(5);
	shaft_angle = shaftAngle();// shaft angle
	
	HAL_Delay(200);
}
/******************************************************************************/
int alignSensor(void)
{
	long i;
	float angle;
	float mid_angle,end_angle;
	float moved;
	
	printf("MOT: Align sensor.\r\n");
	
	// find natural direction
	// move one electrical revolution forward
	for(i=0; i<=500; i++)
	{
		angle = _3PI_2 + _2PI * i / 500.0;
		setPhaseVoltage(voltage_sensor_align, 0,  angle);
		HAL_Delay(2);
	}
	mid_angle=getAngle();
	
	for(i=500; i>=0; i--) 
	{
		angle = _3PI_2 + _2PI * i / 500.0 ;
		setPhaseVoltage(voltage_sensor_align, 0,  angle);
		HAL_Delay(2);
	}
	end_angle=getAngle();
	setPhaseVoltage(0, 0, 0);
	HAL_Delay(200);
	
	printf("mid_angle=%.4f\r\n",mid_angle);
	printf("end_angle=%.4f\r\n",end_angle);
	
	moved =  fabs(mid_angle - end_angle);
	if((mid_angle == end_angle)||(moved < 0.02))  //相等或者几乎没有动
	{
		printf("MOT: Failed to notice movement loop222.\r\n");
		M1_Disable;    //电机检测不正常，关闭驱动
		return 0;
	}
	else if(mid_angle < end_angle)
	{
		printf("MOT: sensor_direction==CCW\r\n");
		sensor_direction=CCW;
	}
	else
	{
		printf("MOT: sensor_direction==CW\r\n");
		sensor_direction=CW;
	}
	
	
	printf("MOT: PP check: ");    //计算Pole_Pairs
	if( fabs(moved*pole_pairs - _2PI) > 0.5 )  // 0.5 is arbitrary number it can be lower or higher!
	{
		printf("fail - estimated pp:");
		pole_pairs=_2PI/moved+0.5;     //浮点数转整形，四舍五入
		printf("%d\r\n",pole_pairs);
  }
	else
		printf("OK!\r\n");
	
	
	setPhaseVoltage(voltage_sensor_align, 0,  _3PI_2);  //计算零点偏移角度
	HAL_Delay(700);
	zero_electric_angle = _normalizeAngle(_electricalAngle(sensor_direction*getAngle(), pole_pairs));
	HAL_Delay(20);
	printf("MOT: Zero elec. angle:");
	printf("%.4f\r\n",zero_electric_angle);
	
	setPhaseVoltage(0, 0, 0);
	HAL_Delay(200);
	
	return 1;
}
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

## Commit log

2023-07-13 首次提交全部文件
    [2804电机.SLDPRT, 4010电机.SLDPRT, ESP32CTRL_AD_PCB.pcbdoc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]
2023-07-15 修正ESP32程序编译错误；补充物料成本清单和部分购买链接；补充部分说明
2023-07-15 添加B站视频链接；补充机械零件选型
2023-07-17 修正Matlab建模错误并通过实机验证
2023-07-18 补充部分说明文档和代码注释
2023-07-23 安卓App修正在安卓12以上闪退问题，替换APK为release版本
2023-07-24 新增低版本Simulink模型文件，支持R2020a及以上版本
2023-08-08 修正Matlab建模脚本错误
2023-11-21 补充部分说明
2023-11-23 修正README行内公式渲染问题

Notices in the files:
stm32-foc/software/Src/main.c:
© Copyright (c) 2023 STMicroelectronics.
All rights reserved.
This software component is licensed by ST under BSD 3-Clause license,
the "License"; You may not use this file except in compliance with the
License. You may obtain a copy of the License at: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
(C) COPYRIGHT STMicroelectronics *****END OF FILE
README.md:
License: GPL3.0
